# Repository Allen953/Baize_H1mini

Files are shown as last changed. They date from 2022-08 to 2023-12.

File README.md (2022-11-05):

# Baize_HexapodRobot_Arduino

$\color{red}{DIY交流群：902595482。}$

实际上这个机械结构是国外老哥做的一款arduino六足机器人。

这里我们结合ROS做运动学解算，做一些控制步态和算法，提供更多丰富的功能。

目前主要用arduino和ros两种软件平台来做，可以用于学习arduino或者ros编程，同时也可以将ros于arduino结合。

arduino端主要跑驱动，ros端跑步态算法等。实际上只要arduino也可以工作，用遥控控制即可。

如下图是实物图：

实物图1

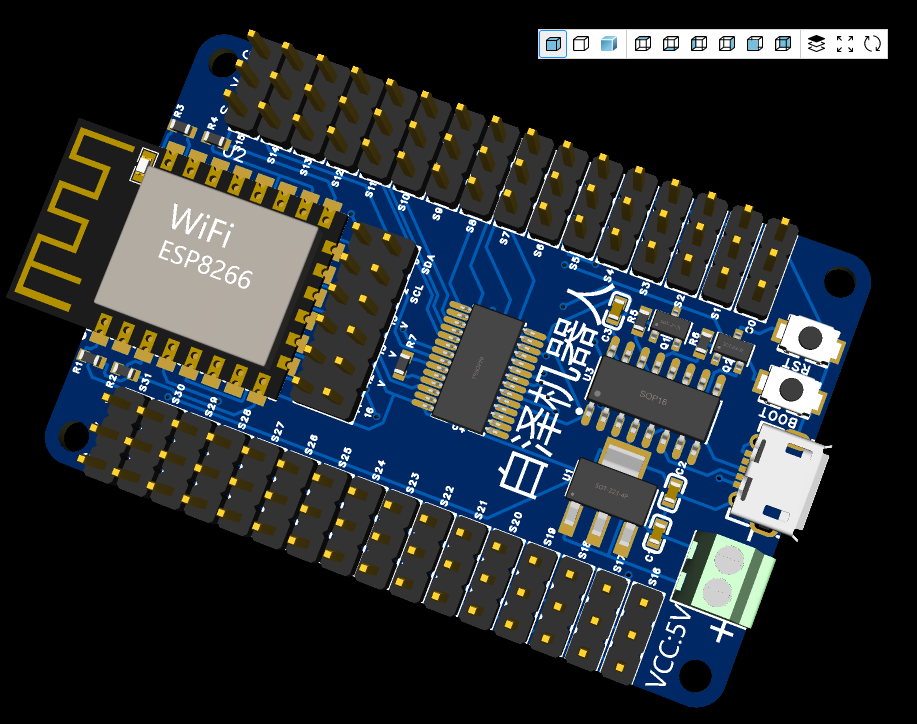
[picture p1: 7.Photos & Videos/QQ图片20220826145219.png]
主控板


ROS下步态规划:

仿真图

俯视图:

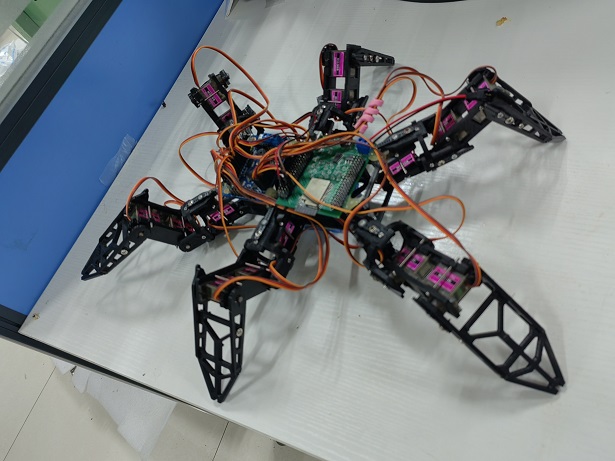
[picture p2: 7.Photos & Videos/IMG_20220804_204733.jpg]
实物图2


RVIZ预览图1
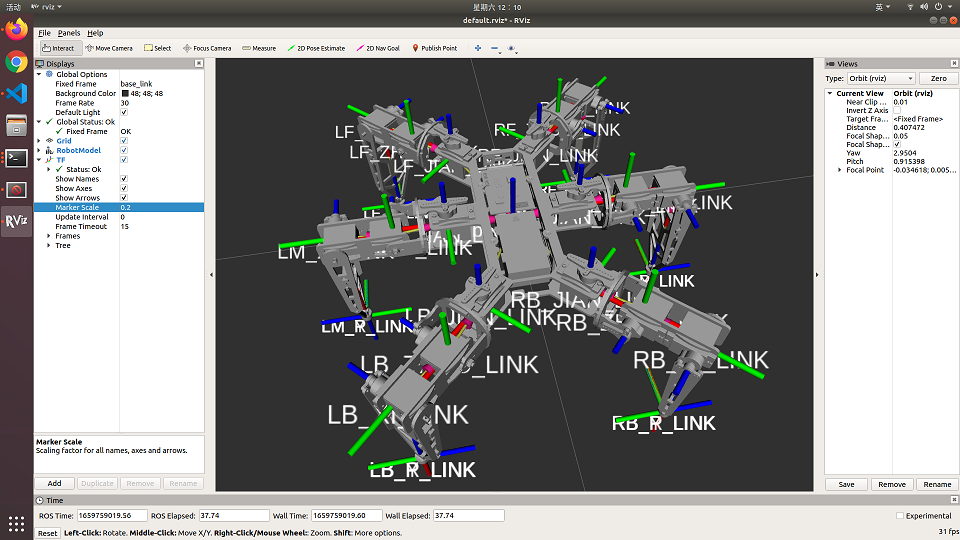
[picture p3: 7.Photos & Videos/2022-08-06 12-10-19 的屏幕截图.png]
RVIZ预览图1


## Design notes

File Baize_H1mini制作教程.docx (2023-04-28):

Baize_H1mini制作教程

作者：Allen

## 一.项目介绍

代码：https://gitee.com/li9535/baize_hexapod-robot

最新代码在这里：

Arduino版：https://github.com/Allen953/Baize_HexapodRobot_Arduino

ROS版：https://github.com/Allen953/Baize_HexapodRobot_ROS

实际上这个机械结构是国外老哥做的一款arduino六足机器人。

这里我们把他改造成ros和arduino两个版本的，提供更多丰富的功能。

下面我们在这个项目后面加上“_arduino”和"_ros"的后缀来区分arduino和ros两个版本。

再在后面加上"_v1"来表示版本号。

例如:“白泽六足机器人_arduino_v1”就是表示这个是arduino版本的第一版。

目前主要用arduino和ros两种软件平台来做，可以用于学习arduino或者ros编程，同时也可以将ros于arduino结合。

最初这个机器人用的也是arduino mega2560当主控，外加一块舵机驱动板，如下图

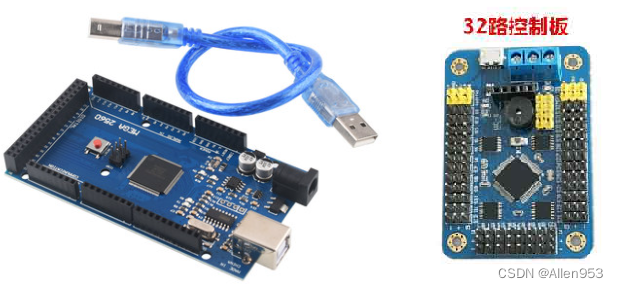
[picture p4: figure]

编辑

在新版本中，我们摒弃传统的开发板+舵机驱动板的方式。开发板+舵机驱动板的方式一个方面是集成度不高，杜邦线接线麻烦且可靠性差。另一个方面，两块板子成本加起来也要将近200块，实在是浪费。

所以我们自己做了两版舵机驱动板，用esp8266或者esp32做主控，更低的成本，更强大的性能，更丰富的功能且支持WiFi无线遥控，实在是香！

他们分别是采用esp8266做主控的Baize_ServoDriver_esp8266 (https://github.com/Allen953/Baize_ServoDriver_esp8266)和采用esp32做主控的Baize_ServoDriver_esp32。

如下图，都是开源的，点击项目名称即可跳转到开源链接。

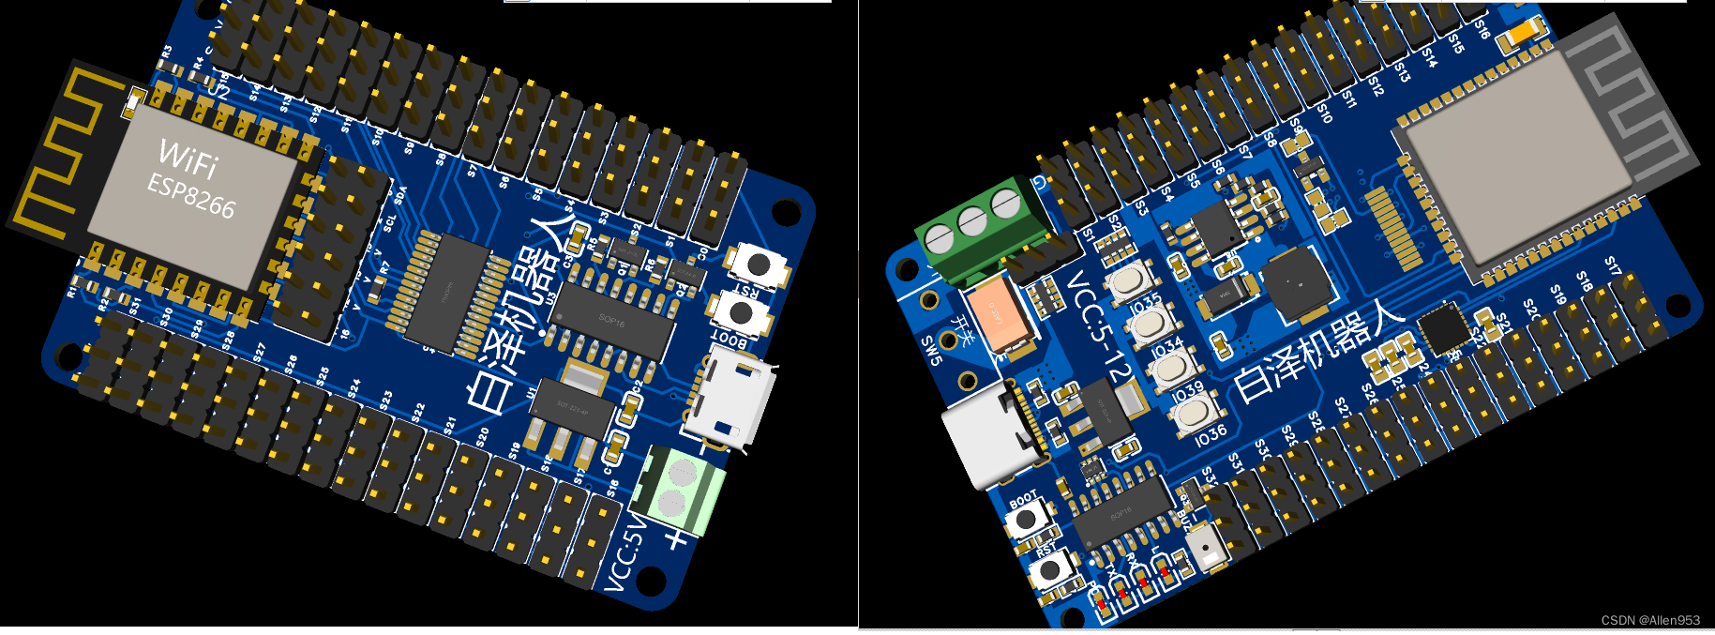
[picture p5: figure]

编辑

实物图

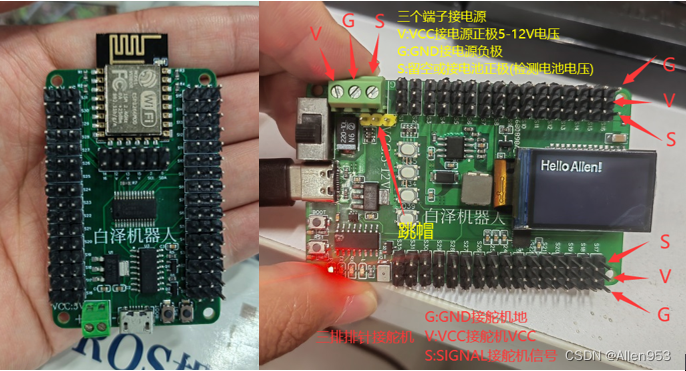
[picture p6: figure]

编辑

两个版本的机器人外观大致如下图所示：

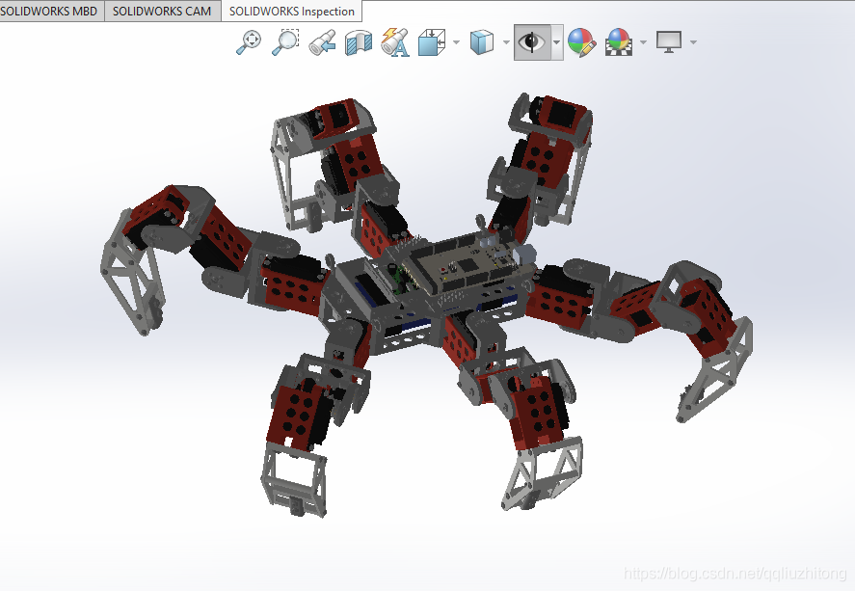
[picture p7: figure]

## 二.Baize_H1mini制作组装机器人机械结构

### 1.组装调试教程

### （1）零件准备 (https://blog.csdn.net/qqliuzhitong/article/details/118224735)

1.主控板x1

Baize_ServoDriver_esp8266 (https://github.com/Allen953/Baize_ServoDriver_esp8266)或者Baize_ServoDriver_esp32 (https://github.com/Allen953/Baize_ServoDriver_esp32)

如下图左边为 Baize_ServoDriver_esp8266；右边为Baize_ServoDriver_esp32

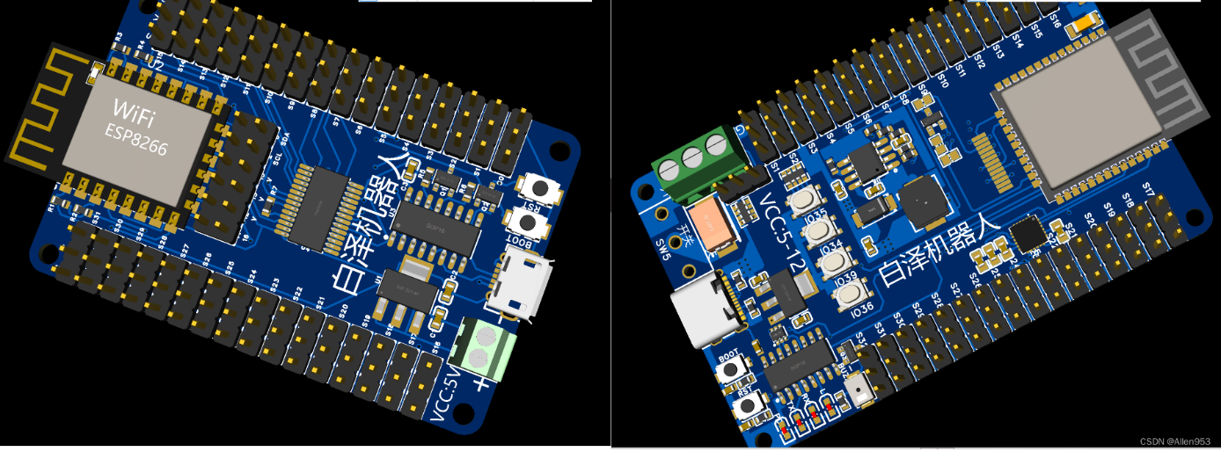
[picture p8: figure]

编辑

建议arduino版六足用Baize_ServoDriver_esp8266而ROS版六足用Baize_ServoDriver_esp32。

我们这里是做arudino版，所以就默认为Baize_ServoDriver_esp8266。

2.机械零件

链接：GitHub - Allen953/Baize_HexapodRobot_Arduino (https://github.com/Allen953/Baize_HexapodRobot_Arduino)

在如下目录下即可下载到

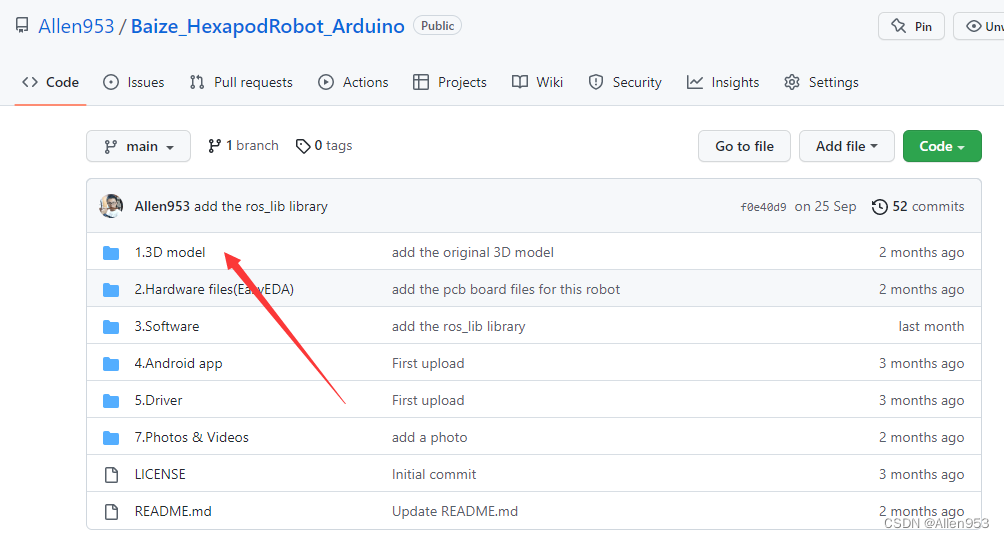
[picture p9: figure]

编辑

编辑

4.舵机x18

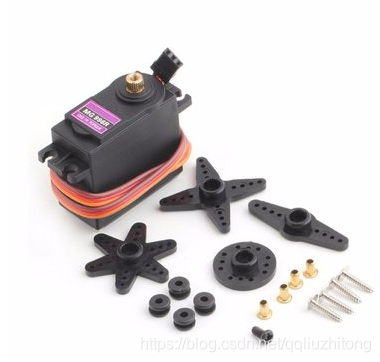
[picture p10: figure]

编辑

5.轴承

624ZZ

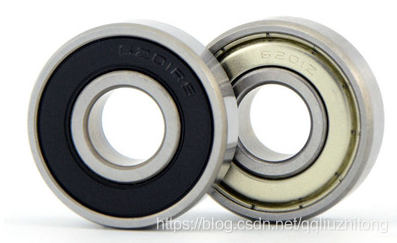
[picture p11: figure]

编辑

6.电池

电池要买大功率电池，7.4V的大电流电池。

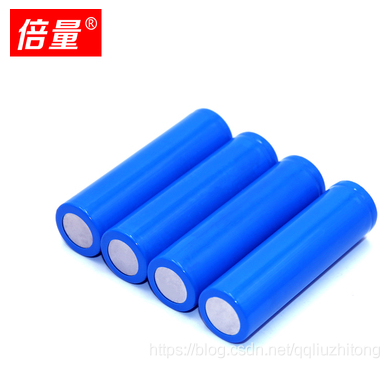
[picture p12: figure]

编辑

7.螺丝

螺丝主要有两种，一种是M3*10，一种是M3*12。下面是螺丝型号及数量。

M3*10——200个

M3*12——200个

### （2）白泽舵机驱动板 (https://blog.csdn.net/qqliuzhitong/article/details/124497060)

这是一块32路舵机驱动板，做舵机机器人非常方便。主控用的esp8266.

电源用的5V的电池，电池直接给舵机供电，经过压降之后产生3.3V电压给esp8266模组供电。

这块板儿主要是用于控制sg90舵机，就是那种蓝色舵机，或者mg90s舵机。

后续会升级，升级后可以控制5-12V的pwm舵机。

这样就可以控制高压的舵机，比如型号为mg996r或mg995的舵机。

3D图片如下图所示：

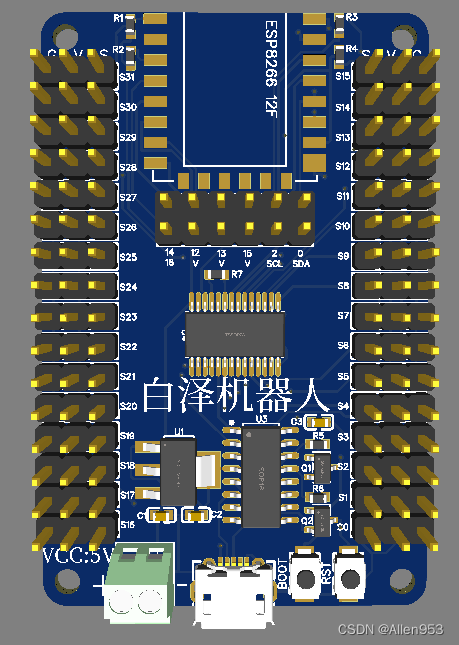
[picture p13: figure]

编辑

实物图如下：

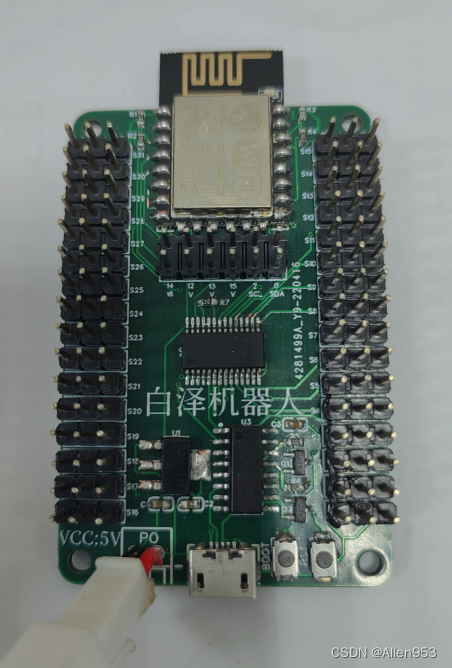
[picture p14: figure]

编辑

#### 测试代码：

#### 例程1：控制32路舵机匀速旋转从0-180度

/*******************************************************

主板：Baize_ServoDriver_esp8266 开源链接：https://github.com/Allen953/Baize_ServoDriver_esp8266

功能：控制32路舵机匀速旋转从0-180度

引脚：SDA:21 SCL:22

Designer: Allen

E-mail:953598974@qq.com

Date:2022-08-24

*******************************************************/

#include <Wire.h>

#include <Adafruit_PWMServoDriver.h>

Adafruit_PWMServoDriver pwm = Adafruit_PWMServoDriver();

Adafruit_PWMServoDriver pwm1 = Adafruit_PWMServoDriver(0x41);

#define SERVOMIN 102 //0.5/20 * 4096 = 102

#define SERVOMAX 512 //2.5/20 * 4096 = 512

void setup() {

Serial.begin(115200);

Serial.println();

Serial.println("16 channel Servo test!");

pwm.begin();

pwm1.begin();

pwm.setPWMFreq(50); // Analog servos run at ~50 Hz updates

pwm1.setPWMFreq(50); // Analog servos run at ~50 Hz updates

delay(200);

for(int i=0;i<16;i++)

{

pwm.setPWM(i, 0, SERVOMIN); // 驱动32路舵机转到0度

pwm1.setPWM(i, 0, SERVOMIN);// 驱动32路舵机转到0度

}

delay(2000);

for (uint16_t pulselen = SERVOMIN; pulselen < SERVOMAX; pulselen++) {

for(int i=0;i<16;i++)

{

pwm.setPWM(i, 0, pulselen);

pwm1.setPWM(i, 0, pulselen);

}

delayMicroseconds(200);

ESP.wdtFeed(); //喂狗防止复位

}

}

void loop() {

}

#### 例程2：控制32路舵机匀速旋转从0-180度，再从180-0度

/*******************************************************

主板：Baize_ServoDriver_esp8266 开源链接：https://github.com/Allen953/Baize_ServoDriver_esp8266

功能：控制32路舵机匀速旋转从0-180度，再从180-0度

引脚：SDA:21 SCL:22

Designer: Allen

E-mail:953598974@qq.com

Date:2022-08-24

*******************************************************/

#include <Wire.h>

#include <Adafruit_PWMServoDriver.h>

Adafruit_PWMServoDriver pwm = Adafruit_PWMServoDriver();

Adafruit_PWMServoDriver pwm1 = Adafruit_PWMServoDriver(0x41);

#define SERVOMIN 102 //0.5/20 * 4096 = 102

#define SERVOMAX 512 //2.5/20 * 4096 = 512

void setup() {

Serial.begin(115200);

Serial.println("16 channel Servo test!");

pwm.begin();

pwm1.begin();

pwm.setPWMFreq(50); // Analog servos run at ~50 Hz updates

pwm1.setPWMFreq(50); // Analog servos run at ~50 Hz updates

}

void loop() {

for (uint16_t pulselen = SERVOMIN; pulselen < SERVOMAX; pulselen++) {

for(int i=0;i<16;i++)

{

pwm.setPWM(i, 0, pulselen);

pwm1.setPWM(i, 0, pulselen);

}

delayMicroseconds(200);

ESP.wdtFeed(); //喂狗防止复位

}

for (uint16_t pulselen = SERVOMAX; pulselen > SERVOMIN; pulselen--) {

for(int i=0;i<16;i++)

{

pwm.setPWM(i, 0, pulselen);

pwm1.setPWM(i, 0, pulselen);

}

delayMicroseconds(200);

ESP.wdtFeed(); //喂狗防止复位

}

}

#### 例程3：控制32路舵机从0，90，180，90，0度之间循环。

/*******************************************************

主板：Baize_ServoDriver_esp8266 开源链接：https://github.com/Allen953/Baize_ServoDriver_esp8266

功能：控制32路舵机从0，90，180，90，0度之间循环

引脚：SDA:21 SCL:22

Designer: Allen

E-mail:953598974@qq.com

Date:2022-08-24

*******************************************************/

#include <Wire.h>

#include <Adafruit_PWMServoDriver.h>

Adafruit_PWMServoDriver pwm = Adafruit_PWMServoDriver();

Adafruit_PWMServoDriver pwm1 = Adafruit_PWMServoDriver(0x41);

#define SERVOMIN 102 //0.5/20 * 4096 = 102

#define SERVOMID 307 //(102+512)/2=307

#define SERVOMAX 512 //2.5/20 * 4096 = 512

//pwm.setPWM(i, 0, pulse);i=0~15对应第0-15个舵机；pwm1.setPWM(j, 0, pulse);j=0~15对应第16-31个舵机，

void setup() {

Serial.begin(115200);

Serial.println("16 channel Servo test!");

pwm.begin();

pwm1.begin();

pwm.setPWMFreq(50); // Analog servos run at ~50 Hz updates

pwm1.setPWMFreq(50); // Analog servos run at ~50 Hz updates

}

void loop() {

//全部舵机转到0度

for(int i=0;i<16;i++)

{

pwm.setPWM(i, 0, SERVOMIN);

pwm1.setPWM(i, 0, SERVOMIN);

}

delayMicroseconds(200);

ESP.wdtFeed(); //喂狗防止复位

delay(1000);

//全部舵机转到90度

for(int i=0;i<16;i++)

{

pwm.setPWM(i, 0, SERVOMID);

pwm1.setPWM(i, 0, SERVOMID);

}

delayMicroseconds(200);

ESP.wdtFeed(); //喂狗防止复位

delay(1000);

//全部舵机转到180度

for(int i=0;i<16;i++)

{

pwm.setPWM(i, 0, SERVOMAX);

pwm1.setPWM(i, 0, SERVOMAX);

}

delayMicroseconds(200);

ESP.wdtFeed(); //喂狗防止复位

delay(1000);

//全部舵机转到90度

for(int i=0;i<16;i++)

{

pwm.setPWM(i, 0, SERVOMID);

pwm1.setPWM(i, 0, SERVOMID);

}

delayMicroseconds(200);

ESP.wdtFeed(); //喂狗防止复位

delay(1000);

}

#### 例程4：板子连到手机热点

手机需要开一个热点，名字："Baize"，密码："baizerobot"。

然后上传这个程序到板子上，在手机上就能看到板子连到手机热点了。

//修改自：https://blog.csdn.net/wangke0809/article/details/70146378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

//原作者：wangke0809

#include <ESP8266WiFi.h>

#define MAX_SRV_CLIENTS 3 //最大同时联接数，即你想要接入的设备数量，8266tcpserver只能接入五个，哎

const char *ssid = "Baize";

const char *password = "baizerobot";

WiFiServer server(8266);//你要的端口号，随意修改，范围0-65535

WiFiClient serverClients[MAX_SRV_CLIENTS];

void setup()

{

Serial.begin(9600);

delay(10);

pinMode(16, OUTPUT);

digitalWrite(16, 0);

WiFi.begin(ssid, password);

while (WiFi.status() != WL_CONNECTED)

{

delay(500);

}

server.begin();

server.setNoDelay(true); //加上后才正常些

}

void loop()

{

blink();

uint8_t i;

if (server.hasClient())

{

for (i = 0; i < MAX_SRV_CLIENTS; i++)

{

if (!serverClients[i] || !serverClients[i].connected())

{

if (serverClients[i]) serverClients[i].stop();//未联接,就释放

serverClients[i] = server.available();//分配新的

continue;

}

}

WiFiClient serverClient = server.available();

serverClient.stop();

}

for (i = 0; i < MAX_SRV_CLIENTS; i++)

{

if (serverClients[i] && serverClients[i].connected())

{

digitalWrite(16, 0);//有链接存在,就一直长亮

if (serverClients[i].available())

{

while (serverClients[i].available())

Serial.write(serverClients[i].read());

}

}

}

if (Serial.available())

{

size_t len = Serial.available();

uint8_t sbuf[len];

Serial.readBytes(sbuf, len);

//push UART data to all connected telnet clients

for (i = 0; i < MAX_SRV_CLIENTS; i++)

{

if (serverClients[i] && serverClients[i].connected())

{

serverClients[i].write(sbuf, len); //向所有客户端发送数据

delay(1);

}

}

}

}

void blink()

{

static long previousMillis = 0;

static int currstate = 0;

if (millis() - previousMillis > 200) //200ms

{

previousMillis = millis();

currstate = 1 - currstate;

digitalWrite(16, currstate);

}

}

#### 例程5：发现（校验）板子上的iic设备

/*******************************************************

主板：Baize_ServoDriver_esp8266 开源链接：https://github.com/Allen953/Baize_ServoDriver_esp8266

功能：扫描IIC总线上挂载的设备

引脚：SDA:21 SCL:22

Designer: Allen

E-mail:953598974@qq.com

Date:2022-08-24

*******************************************************/

#include <Wire.h>

void setup()

{

Wire.begin();

Serial.begin(115200);

}

void loop()

{

byte error, address;

int nDevices;

Serial.println();

Serial.println("Scanning...");

nDevices = 0;

for(address = 1; address < 127; address++ )

{

Wire.beginTransmission(address);

error = Wire.endTransmission();

if (error == 0)

{

Serial.print("I2C device found at address 0x");

if (address<16)

Serial.print("0");

Serial.print(address,HEX);

Serial.println(" !");

nDevices++;

}

else if (error==4)

{

Serial.print("Unknown error at address 0x");

if (address<16)

Serial.print("0");

Serial.println(address,HEX);

}

}

if (nDevices == 0)

Serial.println("No I2C devices found\n");

else

Serial.println("done\n");

delay(5000);

}

#### 例程6：带电压监测的板子测试程序

升级版，主控esp32。供电范围5-12V。当我用7.4V的2S锂电池给舵机供电时，用这个程序来进行板子测试，由于测试时间较长，担心电池过放，所以通过电压监测，当电压过低时，将不再驱动舵机工作。

/***************************************************

对于ARDUINO UNO，这时SCL->A5，SDA - >A4

对于ESP8266，这时SCL->GPIO5，SDA - >GPIO4

****************************************************/

#include <Wire.h>

#include <Adafruit_PWMServoDriver.h>

Adafruit_PWMServoDriver pwm = Adafruit_PWMServoDriver();

Adafruit_PWMServoDriver pwm1 = Adafruit_PWMServoDriver(0x41);

#define SERVOMIN 102 //0.5/20 * 4096 = 102

#define SERVOMAX 512 //2.5/20 * 4096 = 512

//pcb板测试时，如果是2S的锂电池供电，则以此电压为阈值，低于此电压时，不再驱动舵机运动，保护电池。

float voltage_threshold = 6.5;

int voltage_testpin = 26;

float voltage_b = 0.0;

bool servo_f = 1;

void setup() {

Serial.begin(115200);

Serial.println();

Serial.println("16 channel Servo test!");

pwm.begin();

pwm1.begin();

pwm.setPWMFreq(50); // Analog servos run at ~50 Hz updates

pwm1.setPWMFreq(50); // Analog servos run at ~50 Hz updates

delay(200);

for(int i=0;i<16;i++)

{

pwm.setPWM(i, 0, SERVOMIN); // 驱动32路舵机转到0度

pwm1.setPWM(i, 0, SERVOMIN);// 驱动32路舵机转到0度

}

delay(2000);

for (uint16_t pulselen = SERVOMIN; pulselen < SERVOMAX; pulselen++) {

for(int i=0;i<16;i++)

{

pwm.setPWM(i, 0, pulselen);

pwm1.setPWM(i, 0, pulselen);

}

delayMicroseconds(200);

}

}

void loop() {

if(servo_f==1)

{

for (uint16_t pulselen = SERVOMIN; pulselen < SERVOMAX; pulselen++) {

for(int i=0;i<16;i++)

{

pwm.setPWM(i, 0, pulselen);

pwm1.setPWM(i, 0, pulselen);

}

delayMicroseconds(200);

}

//电压检测

int voltage_sum = 0.0;

for(int i=0;i<10;i++)

{

voltage_sum += float(analogRead(voltage_testpin))/4095.0*3.3*4.0;

Serial.println(analogRead(voltage_testpin));

delay(100);

}

voltage_b = voltage_sum / 10.0;

Serial.println(voltage_b);

if(voltage_b<voltage_threshold)

servo_f = 0;

for(int i=0;i<16;i++)

{

pwm.setPWM(i, 0, SERVOMIN); // 驱动32路舵机转到0度

pwm1.setPWM(i, 0, SERVOMIN);// 驱动32路舵机转到0度

}

delay(2000);

}

}

#### 例程7：串口控制舵机角度

/*******************************************************

主板：Baize_ServoDriver_esp8266 开源链接：https://github.com/Allen953/Baize_ServoDriver_esp8266

功能：串口输入角度，板子驱动舵机转到该角度

引脚：SDA:21 SCL:22

Designer: Allen

E-mail:953598974@qq.com

Date:2022-08-24

*******************************************************/

#include <Wire.h>

#include <Adafruit_PWMServoDriver.h>

Adafruit_PWMServoDriver pwm = Adafruit_PWMServoDriver(); //驱动1~16或(0~15)号舵机

Adafruit_PWMServoDriver pwm1 = Adafruit_PWMServoDriver(0x41); //驱动17~32或(16~31)号舵机

//#define SERVOMIN 102 //0.5/20 * 4096 = 102

//#define SERVOMID 307 //1.5/20 * 4096 = 307

//#define SERVOMAX 512 //2.5/20 * 4096 = 512

//实际测试

#define SERVOMIN 102

#define SERVOMID 327

#define SERVOMAX 552

void setup() {

// put your setup code here, to run once:

Serial.begin(115200);

pwm.begin();

pwm1.begin();

pwm.setPWMFreq(50); // Analog servos run at ~50 Hz updates

pwm1.setPWMFreq(50); // Analog servos run at ~50 Hz updates

}

void loop() {

// put your main code here, to run repeatedly:

while(!(Serial.available()>0))ESP.wdtFeed();//喂狗防止复位

int pwmsum=Serial.parseInt();

for(int i=0;i<16;i++)

{

pwm.setPWM(i, 0, pwmsum);

}

pwm1.setPWM(0, 0, pwmsum);

pwm1.setPWM(1, 0, pwmsum);

delay(100);

}

#### 固件烧录

有些小伙伴没有安装好arduino ide或者没有安装好esp8266的硬件支持包，这个时候呢，就没法编译程序进行烧录了。

所以我在资料文件夹里面放上了编译好的固件，咱们就无需编译直接使用烧录工具就可以把固件给烧录到板子上了。

找到烧录工具并打开

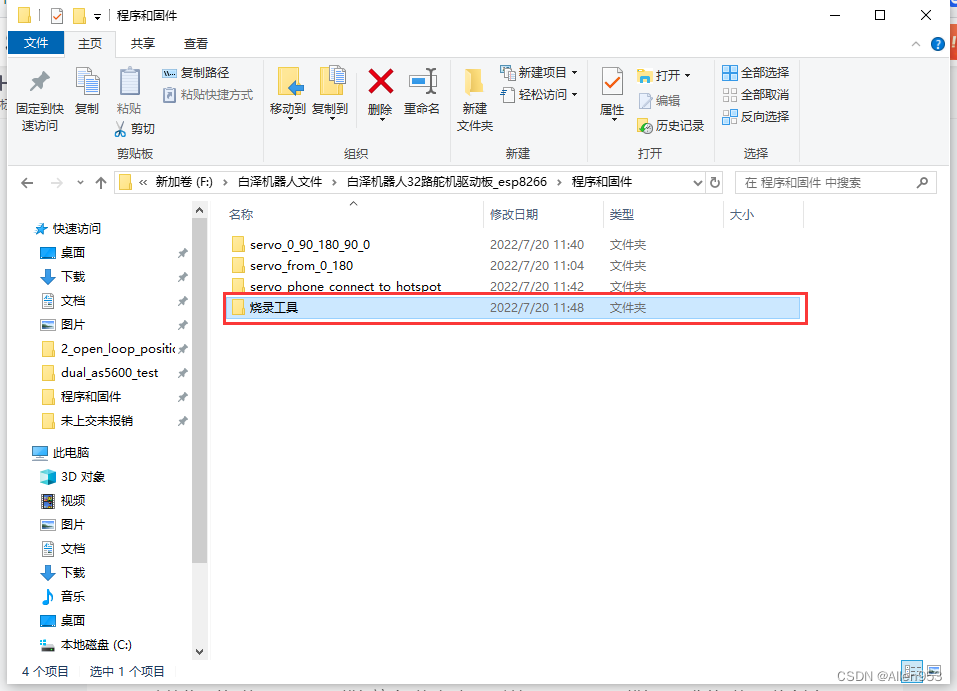
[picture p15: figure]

编辑

打开烧录程序

编辑

选中com口

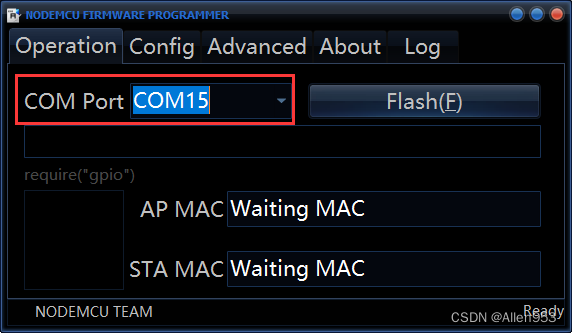
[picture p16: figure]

编辑

点击齿轮选中要烧录的固件(.bin格式)，填写烧录地址，并在要烧录的固件前面打勾。

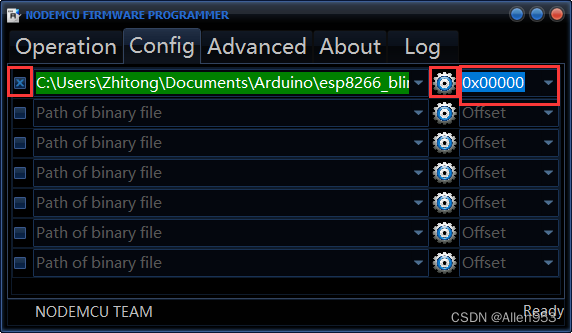
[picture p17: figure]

编辑

选择上传的波特率，flash大小，flash速度等。

然后点击flash进行烧录，烧录完成后，进度条会跑满，左下角会出现绿色打勾符号。

按一下板子上的rst按键，重启板子，程序就开始执行了。

#### 我遇到的问题

##### 1.插电脑不出com口，怎么操作都没用

ch340芯片焊错了，焊成了ch340g芯片，导致usb-ttl芯片无法正常工作。

##### 2.插电脑不出com口，按住rst按键会出com口，松开又消失

原因是台式机电脑前面的usb口能供应的电流太小了，带不起来板子。

当按住rst的时候，esp8266模组这个时候相当于是关机了，esp8266模组不工作的时候，整个板子自然功耗下降下来，然后ch340c芯片工作正常，这样一来电脑就出com口了。

而一旦松开rst，这个时候esp8266模组要开始工作，板子功耗又起来了，usb口带不动过载了，所以ch340c芯片无法正常工作，com口就消失了。

### （3）3D打印开源六足机器人程序 (https://blog.csdn.net/qqliuzhitong/article/details/116492164)

### 2.编程例程

持续更新中！！！！！！！

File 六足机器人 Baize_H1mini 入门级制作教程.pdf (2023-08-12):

# 六足机器人 Baize_H1mini 入门级制作教程

## 作者：人民群众

版本：20230723

Baize_H1mini 六足机器人是一个创客学习平台，通过该学习平台，可以学 习 mixly 图形化编程，Arduino 平台的 C 语言编程，ROS 机器人编程，也可以学 习一些传感器的控制。
在 Baize_H1mini 中，我们摒弃传统的开发板+舵机驱动板的方式。开发板+ 舵机驱动板的方式一方面集成度不高，杜邦线接线麻烦且可靠性差；另一方面， 集成板降低了电器元件的成本，让机器人制作更加方便。

我们有一个 QQ 交流群：902595482，可以进来互相学习。 jiaoliuqun:902595482

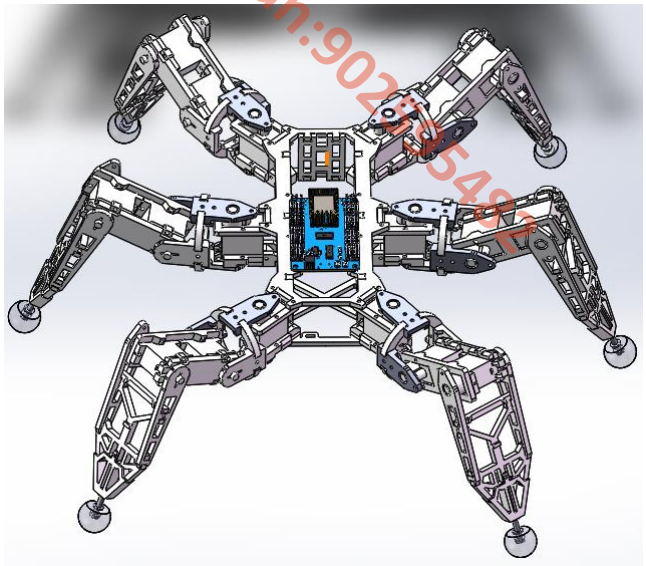
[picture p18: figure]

### 重要提示

1.电池一定要小心接，最好反复确认自己理解了电源部分是怎么接线

的，然后再通电；否则不能随便通电，以免短路起火或发生爆炸。

2.对于新手来讲，一定要认真阅读理解本教程，不能一目十行不仔细

阅读文字说明只看图片，这将会导致很多步骤理解不到。

3.在碰到不懂且说明书上没有的内容时，一定要善于用百度进行搜索 且多多尝试。jiaoliuqun:902595482 （也可以在群里问，推荐在群里提问！）

### 一.项目介绍

1.项目介绍

最新代码在这里：https://github.com/Allen953/Baize_H1mini 实际上这个机械结构是国外老哥做的一款 arduino 六足机器人。 这里我们把他改造成 arduino 版本的，提供更多丰富的功能。目前主要用 arduino 和 ros 两种软件平台来做，可以用于学习 arduino 或者 ros 编程，同时 也可以将 ros 于 arduino 结合。
在这个六足机器人的制作中，我们摒弃传统的开发板+舵机驱动板的方式。

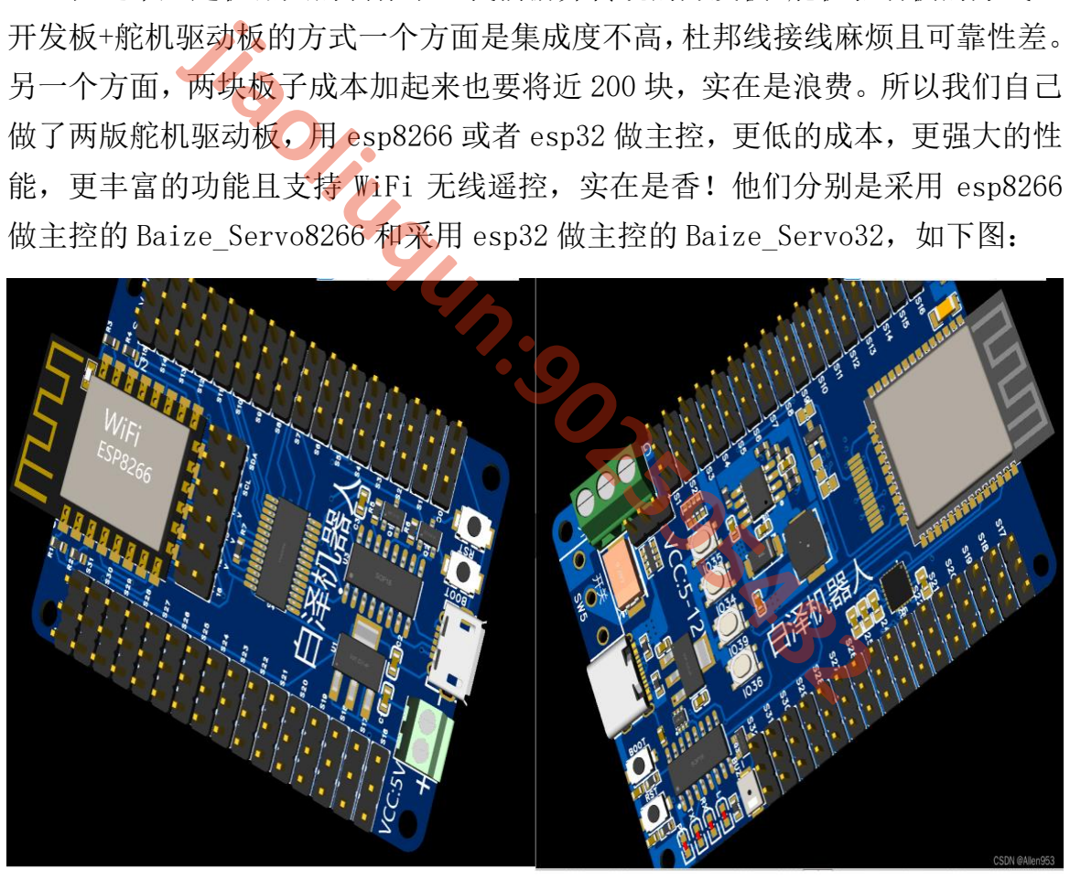
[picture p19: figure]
jiaoliuqun:902595482

开发板+舵机驱动板的方式一个方面是集成度不高，杜邦线接线麻烦且可靠性差。 另一个方面，两块板子成本加起来也要将近 200 块，实在是浪费。所以我们自己 做了两版舵机驱动板，用 esp8266 或者 esp32 做主控，更低的成本，更强大的性 能，更丰富的功能且支持 WiFi 无线遥控，实在是香！他们分别是采用 esp8266 做主控的 Baize_Servo8266 (https://github.com/Allen953/Baize_ServoDriver_esp8266) 和采用 esp32 做主控的 Baize_Servo32，如下图： (https://github.com/Allen953/Baize_ServoDriver_esp32)

实物图

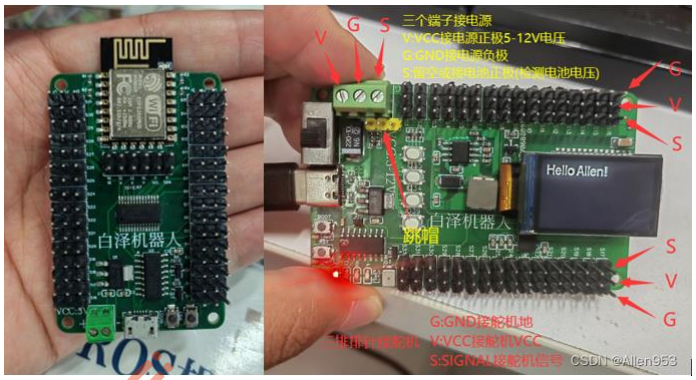
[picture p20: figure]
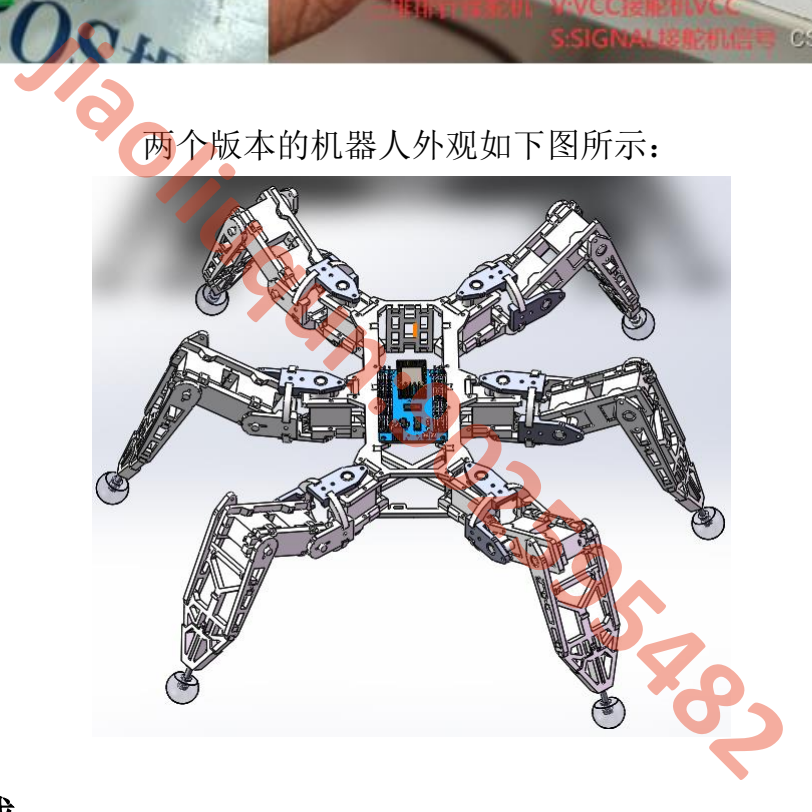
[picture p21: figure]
jiaoliuqun:902595482

两个版本的机器人外观如下图所示：

2.资料下载

在开始制作该项目前，最好将所有的资料先下载到自己的电脑上，你需要按 照以下步骤来下载该项目需要用到的全部资料：
首 先 访 问 项 目 网 页 ： https://github.com/Allen953/Baize_H1mini

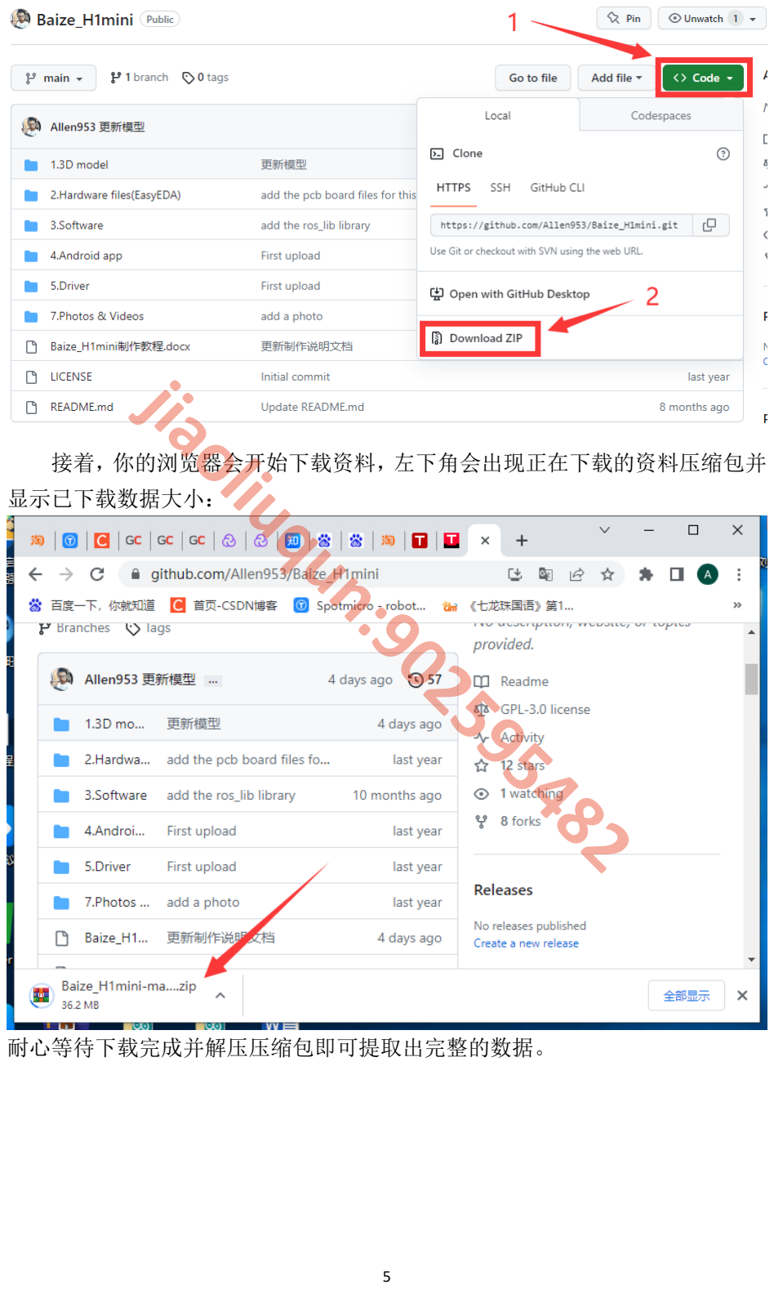
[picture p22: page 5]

接着，你的浏览器会开始下载资料，左下角会出现正在下载的资料压缩包并 显示已下载数据大小：

耐心等待下载完成并解压压缩包即可提取出完整的数据。

# jiaoliuqun:902595482

二.Baize_H1mini 机器人零件制作准备

1.机械结构零件打印制作

重要提示：自己使用打印机打印零件时，对于新手来说肯定会由于参数设置 问题将零件打废，因此要仔细配置参数确保参数正确。对于需要添加支撑的零 件，一定要记得添加支撑。
首先要找到零件的图纸，打开我们刚刚下载的整个项目资料文件夹，找到如 下路径 1.3D model\Baize_HexapodRobot_Arduino_3DPrinter\STL Files，可以 看到该文件夹下有很多可以打印的 STL 格式图纸，如下图红框中所示：

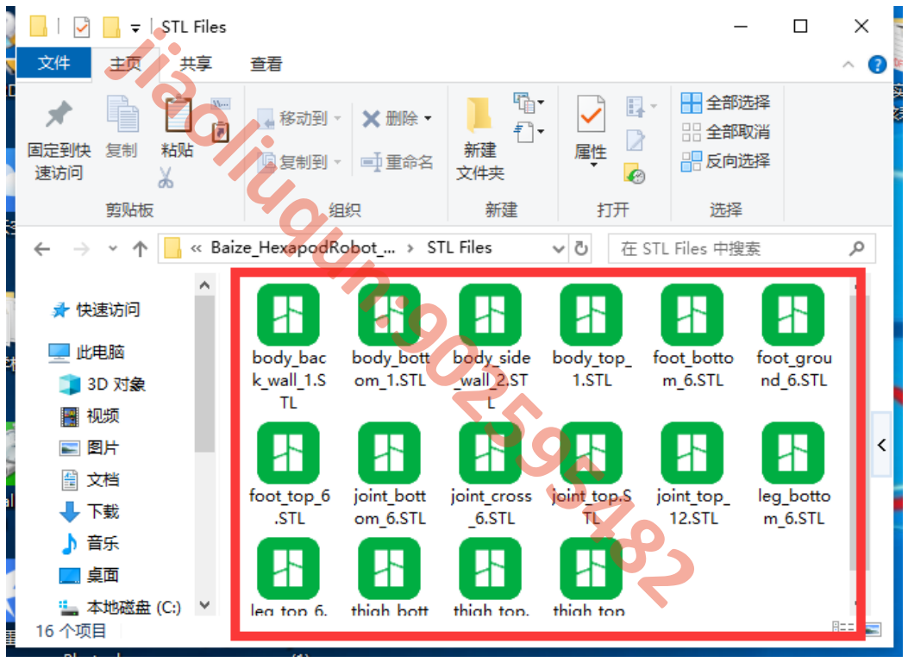
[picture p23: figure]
jiaoliuqun:902595482

接下来就可以开始打印了，我这里用的是拓竹 P1P 型号 3D 打印机，因此下 面的打印教程也是用该款型号打印机制作的，如果你用的其他型号的 3D 打印机， 则可以一次做参考并参照自己 3D 打印机的说明书进行打印。
下载 Bambu Studio：http:bambulab.com/download
登录 Bambu Stidio，新建或打开一个项目。

添加一个模型进行模型切片。
完成模型切片后，选择打印机并发送打印。
打印板类型选择纹理 PEI 打印板

打印材料是啥？ PLA 3D 打印材料一般有 PLA 和 ABS 两款材料

这里需要选择打印材料。

# jiaoliuqun:902595482

2.主控板 PCB 制作及焊接

3.标准件准备（包括螺丝和电器原件等）

1..舵机 x18

2.电池

电池要买 18650 大功率电池，单节电池是 3.7V 左右（之所以说是 3.7V 左右 而不是 3.7V 是因为电池电压随着使用过程会发生改变，当单节电池充满电时大 多数在 4.2V 左右，当电池放电到没电状态之后，电池电压会下降到 3.7V 甚至 3.2V，电池电压下降到 3.2V 的时候就要充电了，如果电池电压下降太多，可能

# jiaoliuqun:902595482

会发生永久性的损坏充不了电，因此在使用过成功要及时为电池充电以免电池损 坏），这里我们两节串联起来使用，加起来就是 7.2V 左右。

3.螺丝等标准件

螺丝一共有以下几种：下面是螺丝型号及数量
M2*30——36 个
M2*8——12 个
M2*15——6 个
M2*5——42 个
圆柱销φ4*12——18 个

4.LM2596S 压降模块

这个压降模块可以将 2 节 18650 电池的 7.4~8.4V 电压降至 5V 电压，由于我

们的板子供电电压是 5V，而且舵机供电电压也是 5V，因此需要用到这个模块。 jiaoliuqun:902595482

# jiaoliuqun:902595482

三.Baize_H1mini 机器人组装

1.零件准备 (https://blog.csdn.net/qqliuzhitong/article/details/118224735)

1.主控板 x1
Baize_ServoDriver_esp8266 (https://github.com/Allen953/Baize_ServoDriver_esp8266) 或者 Baize_ServoDriver_esp32 (https://github.com/Allen953/Baize_ServoDriver_esp32)
如下图左边为 Baize_ServoDriver_esp8266 ；右边为 Baize_ServoDriver_esp32

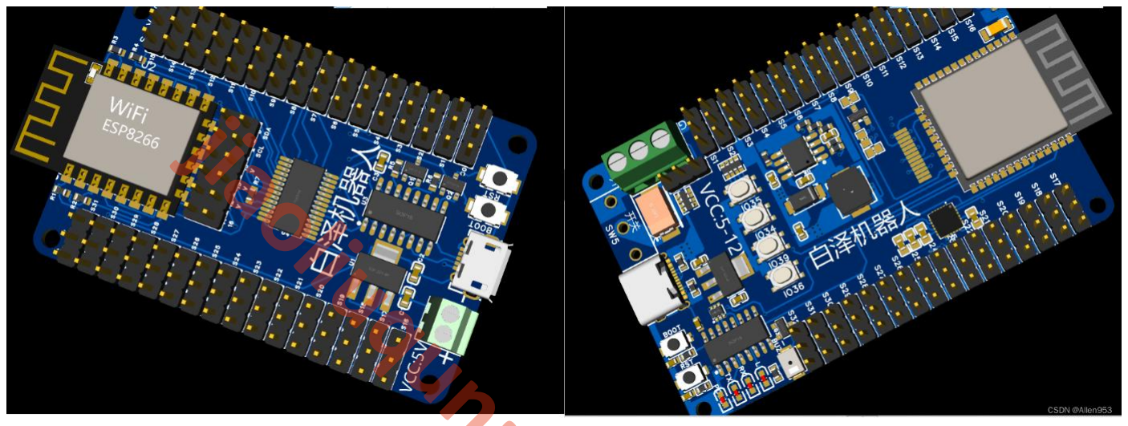
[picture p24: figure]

建议 arduino 版六足用 Baize_ServoDriver_esp8266 而 ROS 版六足用 Baize_ServoDriver_esp32。
我们这里是做 arudino 版，所以就默认为 Baize_ServoDriver_esp8266。

2.机械零件

链接：https://github.com/Allen953/Baize_H1mini

在如下目录下即可下载到 jiaoliuqun:902595482

2.组装教程

找到下面的φ4*12 的金属圆柱销，然后将圆柱销用力塞进或者敲进打印的零件 里面

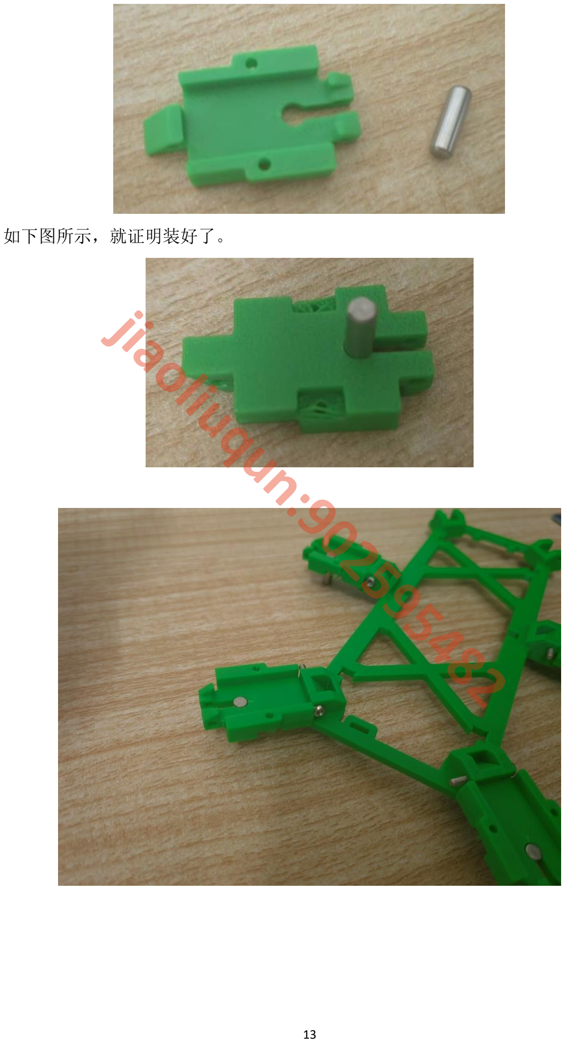
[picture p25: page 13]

如下图所示，就证明装好了。

# jiaoliuqun:902595482

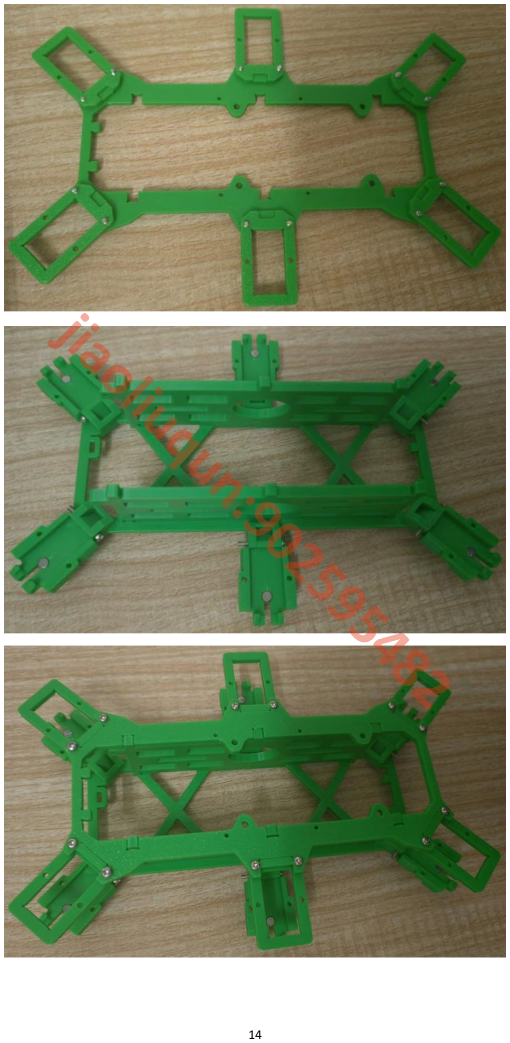
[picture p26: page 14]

# jiaoliuqun:902595482

3.电路焊接

首先，需要找一个 18650 电池的电池盒，由于电池盒上面直接引出来了两条 线，这两条电源线是先输入到 LM2596S 这个压降模块的，需要先降压到 5V。由 于直接把电池盒上面的两条电源线焊接在 LM2596S 模块上那就进行了通电，而无 法断电，因此需要一个开关。我们现在的做法是在电池的输出端和 LM2596S 的输 入端各焊一个插接口的电源线，这样可以通过插拔的方式给整个电路通电和断电， 起到开关的作用。

接着需要焊接 LM2596S 的输入和输出线

LM2596S 压降模块的作用就是把电压降至 5V，电流从电池里面出来的时候是 7.4V， 进入该模块的时候也是 7.4V，从该模块出来的时候，电压就变成 5V 了，就可以 输入到机器人板子上了。整个电源部分工作原理如下图所示,LM2596S 模块的 IN+ 表示输入正极，IN-表示输入负极，也就是电池的电从这两个地方输入到模块； OUT+表示的是输出负极，OUT-表示的是输出正极，输出的 5V 电压从这里流出去。

电源线红色是正极，黑色是负极。

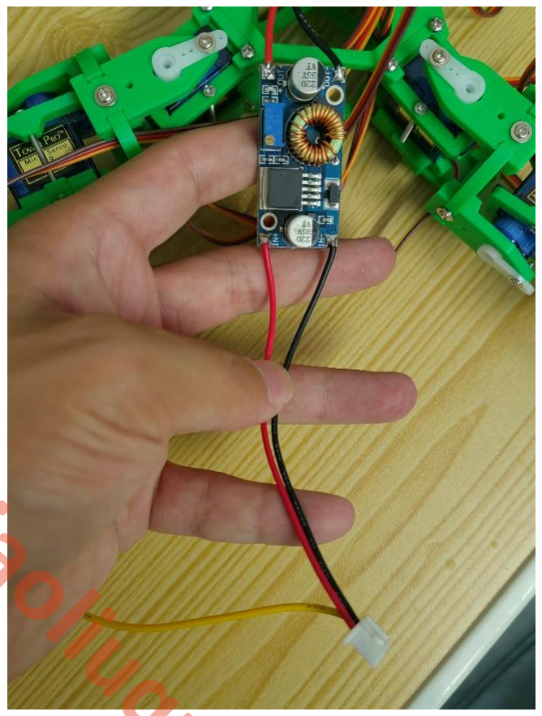
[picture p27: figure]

接下来，就可以直接把电池的输出接口插在 LM2596 的输入接口了，这个时 候先别着急把 LM2596S 模块的输出接口接到舵机控制板上面，如下图所示，红色 打叉号的两条线先断开别接上。因为 LM2596S 模块的输出电压我们还没调节，默 认情况下 LM2596S 模块的输出电压太高，我们如果直接将 LM2596S 的输出线路接 入舵机控制板，则会烧毁我们的舵机控制板，因此需要现行调节 LM2596S 模块的

# 输出电压。 jiaoliuqun:902595482


固定电池：jiaoliuqun:902595482

如下图所示，首先需要将电压调至 5V。接着再给机器人通电，如果通电测 试正常，则可以将机器人电源板固定好。


固定压降模块，注意别让该模块挡住主控板的 micro usb 口，我这里就挡住 了口，不方便烧录代码了。


固定主板：

4.舵机接线

接线的话，按照如下图所示进行接线即可。就是右腿第一个舵机接到板子的 第一个口上面，注意有的板子是从 0 开始有的板子是从 1 号开始，如果板子上面 的舵机标号从 0 开始就从 0 开始接线，如果板子上面的舵机标号从 1 开始就从 1


开始接线。

# jiaoliuqun:902595482

四.Baize_H1mini 机器人代码烧录调试

1.Arduino IDE 配置 ESP8266 开发板

这一步主要是在arduino ide里面添加esp8266的硬件支持，我们默认安装完arduino之后， arduino 里的开发板选项是没有 esp8266 的，因此需要添加硬件支持，让 arduino ide 可以 支持 esp8266 开发板。首先打开 Arduino IDE，点击文件——首选项

jiaoliuqun:902595482

接下来会跳出下方界面，点击箭头 1 所示的那个白色小方框，接着会跳出箭头 2 所示的小窗 口，将该网址——http://arduino.esp8266.com/stable/package_esp8266com_index.json，复制 粘贴到小窗口里面，如图 3 所示，保证这个网址在里面就可以了，然后点击箭头 4 所示的好 即可。


接下来，点击 Arduino IDE 上方的工具——开发板——开发板管理器

接着会跳出来如下窗口，在箭头 1 所示的窗口中输入 esp8266 并敲下回车按钮进行开发板搜 索，接着将会出现图中的 esp8266 选项，点击箭头 2 所示的版本选择最新的版本，根据箭头 3 点击安装即可开始安装，等待进度条完成安装即可。

# jiaoliuqun:902595482


接着，我们在工具——开发板选项里面，就可以看到 esp8266 开发板了，我们选择如下图所 示的开发板即可。

2.配置库文件

在配置了开发板之后，还需要配置我们项目需要用到的库文件，这样我们的程序代码才能正 常编译烧录。
编译是程序编程机器代码的过程，计算机只能直接理解机器代码，我们编写的程序它是不能 直接理解的，因此我们写的程序都需要进行编译计算机才能理解。 烧录是将编译后的程序从电脑上上传到机器人板子上面的芯片里面的过程，只有将程序上传

# jiaoliuqun:902595482

到机器人的板子上面，程序才能正确执行并且控制机器人运行。 找到如下文件夹：

将其复制到自己电脑的如下文件夹里面：

3.烧录代码

烧录代码前，首先根据如下步骤，一步一步通过文件路径找到我们需要的代 码文件。
首先打开 3.Software 这个文件夹

然后打开 Arduino 主程序这个文件夹

# jiaoliuqun:902595482

接着再打开第一个 Baize_HexapodRobot_Arduino 文件夹

然后找到 Baize_HexapodRobot_Arduino.ino 这个程序文件，找到之后可以 双击直接打开。

打开后的界面如下图所示： jiaoliuqun:902595482

接下来，我们选择开发板类型，然后通过软件的验证功能看程序代码是否有 格式错误。
选择开发板类型如下：


然后点击软件界面的验证按钮，可以看到如图，下面出现编译完成的提示，

说明我们的代码没有问题，并且已经通过了编译。 jiaoliuqun:902595482

接下来，我们将开发板通过 Micro USB 线连接到电脑上。
注意：当通过 Micro USB 线连接开发板和电脑时，开发板上不能连接任何舵 机，否则可能烧坏电脑主板。

接下来，点击上传按钮，即可把程序上传到开发板上面。 jiaoliuqun:902595482

五.Baize_H1mini 机器人手机 APP 遥控配置

在测试前，首先需要给你的手机安装一个遥控软件并且进行相应的设置，我 们这里安装的遥控软件名字是 NeTorch，如果你的应用市场可以直接搜到的话， 可以直接在应用市场进行安装。

如果应用市场搜索不到的话，可以将这个软件安装包发送到自己的安卓手机 上，然后再进行安装。
软件安装包位置如下图所示，首先找到 4.Android app 这个文件夹。

如下图所示的 NeTorch.apk 就是我们需要找到的手机遥控软件安装包，你可 以通过 QQ 或者微信将安装包发送到手机上进行安装。

安装之后打开如下图所示：


接下来，需要你用自己的手机开个热点。
热点名字(SSID)是：Baize
热点密码(PASS)是：baizerobot
接下来需要给机器人通电，机器人通电之后，可看到主板上有个蓝灯亮起来 了。
如果蓝灯过几秒之后变为闪烁状态，则代表着机器人主板已经连接到了手机 热点，网络连接正常。
接下来可以设置手机遥控 APP 进行遥控了。
首先需要你查看一下机器人的 IP 地址，点击个人热点之后，可以看到有一 个设备连接了你的手机，这里可以看到如下图所示界面，我们可以看到这个 IP

地址为：192.168.43.227，这里需要你先记下这个 IP 地址。 jiaoliuqun:902595482


然后打开 Netorch 软件界面，进行相应的设置：

然后我们设置按钮：
首先点击按钮模式，接下来长按按钮就可以进行按钮的设置了。我们点开按 钮把相应的前后左右设置好，按照如下图完成按钮的设置。

# jiaoliuqun:902595482


控制指令表如下：
控制指令表
指令 | 动作 | 指令 | 动作
a | 前进行走 | f | 向左横移
b | 后退行走 | g | 向右横移
c | 原地左转 | h | 步态切换
d | 原地右转 | i | 身高切换
e | 停止

后续会更新更多动作指令！

# jiaoliuqun:902595482

接下来便可以进行遥控操作测试了，点击一下前进的按钮，是不是已经发现 机器人开始前进了呢？
接下来可以愉快的玩耍了。

# jiaoliuqun:902595482

### 六.白泽舵机驱动板 (https://blog.csdn.net/qqliuzhitong/article/details/124497060)

这是一块 32 路舵机驱动板，做舵机机器人非常方便。主控用的 esp8266。 电源用的 5V 的电池，电池直接给舵机供电，经过压降之后产生 3.3V 电压给 esp8266 模组供电。
这块板儿主要是用于控制 sg90 舵机，就是那种蓝色舵机，或者 mg90s 舵机。 后续会升级，升级后可以控制 5-12V 的 pwm 舵机。 这样就可以控制高压的舵机，比如型号为 mg996r 或 mg995 的舵机。 3D 图片如下图所示：

实物图如下：jiaoliuqun:902595482

测试代码：

例程 1：控制 32 路舵机匀速旋转从 0-180 度

/*******************************************************
主板：Baize_ServoDriver_esp8266 | 开源链接：
https://github.com/Allen953/Baize_ServoDriver_esp8266 功能：控制 32 路舵机匀速旋转从 0-180 度
引脚：SDA:21 SCL:22
Designer: Allen
E-mail:953598974@qq.com
Date:2022-08-24
*******************************************************/

#include <Wire.h>

#include <Adafruit_PWMServoDriver.h>

Adafruit_PWMServoDriver pwm = Adafruit_PWMServoDriver(); Adafruit_PWMServoDriver pwm1 = Adafruit_PWMServoDriver(0x41);

#define SERVOMIN 102 | //0.5/20 * 4096 = 102

#define SERVOMAX 512 | //2.5/20 * 4096 = 512

void setup() {
Serial.begin(115200);
Serial.println();
Serial.println("16 channel Servo test!");

pwm.begin();
pwm1.begin();
pwm.setPWMFreq(50); // Analog servos run at ~50 Hz updates pwm1.setPWMFreq(50); // Analog servos run at ~50 Hz updates

delay(200);
for(int i=0;i<16;i++)
{
pwm.setPWM(i, 0, SERVOMIN); // 驱动 32 路舵机转到 0 度 pwm1.setPWM(i, 0, SERVOMIN);// 驱动 32 路舵机转到 0 度

# jiaoliuqun:902595482

}
delay(2000);
for (uint16_t pulselen = SERVOMIN; pulselen < SERVOMAX; pulselen++) { for(int i=0;i<16;i++)
{
pwm.setPWM(i, 0, pulselen); pwm1.setPWM(i, 0, pulselen);
}
delayMicroseconds(200);
ESP.wdtFeed(); | //喂狗防止复位
}
}

void loop() {

}

例程 2：控制 32 路舵机匀速旋转从 0-180 度，再从 180-0 度

/*******************************************************
主板：Baize_ServoDriver_esp8266 | 开源链接：
https://github.com/Allen953/Baize_ServoDriver_esp8266 功能：控制 32 路舵机匀速旋转从 0-180 度，再从 180-0 度 引脚：SDA:21 SCL:22
Designer: Allen
E-mail:953598974@qq.com
Date:2022-08-24
*******************************************************/

#include <Wire.h>

#include <Adafruit_PWMServoDriver.h>

Adafruit_PWMServoDriver pwm = Adafruit_PWMServoDriver(); Adafruit_PWMServoDriver pwm1 = Adafruit_PWMServoDriver(0x41);

#define SERVOMIN 102 | //0.5/20 * 4096 = 102

#define SERVOMAX 512 | //2.5/20 * 4096 = 512

void setup() {
Serial.begin(115200);
Serial.println("16 channel Servo test!");

# jiaoliuqun:902595482

pwm.begin();
pwm1.begin();
pwm.setPWMFreq(50); // Analog servos run at ~50 Hz updates pwm1.setPWMFreq(50); // Analog servos run at ~50 Hz updates }

void loop() {
for (uint16_t pulselen = SERVOMIN; pulselen < SERVOMAX; pulselen++) {
for(int i=0;i<16;i++)
{
pwm.setPWM(i, 0, pulselen); pwm1.setPWM(i, 0, pulselen);
}
delayMicroseconds(200);
ESP.wdtFeed(); | //喂狗防止复位
}
for (uint16_t pulselen = SERVOMAX; pulselen > SERVOMIN; pulselen--) {
for(int i=0;i<16;i++)
{
pwm.setPWM(i, 0, pulselen); pwm1.setPWM(i, 0, pulselen);
}
delayMicroseconds(200);
ESP.wdtFeed(); | //喂狗防止复位
}
}

例程 3：控制 32 路舵机从 0，90，180，90，0 度之间循环。

/*******************************************************
主板：Baize_ServoDriver_esp8266 | 开源链接：
https://github.com/Allen953/Baize_ServoDriver_esp8266 功能：控制 32 路舵机从 0，90，180，90，0 度之间循环 引脚：SDA:21 SCL:22
Designer: Allen
E-mail:953598974@qq.com
Date:2022-08-24
*******************************************************/

#include <Wire.h>

# jiaoliuqun:902595482

#include <Adafruit_PWMServoDriver.h>

Adafruit_PWMServoDriver pwm = Adafruit_PWMServoDriver(); Adafruit_PWMServoDriver pwm1 = Adafruit_PWMServoDriver(0x41);

#define SERVOMIN 102 | //0.5/20 * 4096 = 102

#define SERVOMID 307 | //(102+512)/2=307

#define SERVOMAX 512 | //2.5/20 * 4096 = 512

//pwm.setPWM(i, 0, pulse);i=0~15 对应第 0-15 个舵机；pwm1.setPWM(j, 0, pulse);j=0~15 对应第 16-31 个舵机，

void setup() {
Serial.begin(115200);
Serial.println("16 channel Servo test!");

pwm.begin();
pwm1.begin();
pwm.setPWMFreq(50); // Analog servos run at ~50 Hz updates pwm1.setPWMFreq(50); // Analog servos run at ~50 Hz updates }

void loop() {
//全部舵机转到 0 度
for(int i=0;i<16;i++)
{
pwm.setPWM(i, 0, SERVOMIN); pwm1.setPWM(i, 0, SERVOMIN);
}
delayMicroseconds(200);
ESP.wdtFeed(); | //喂狗防止复位
delay(1000);
//全部舵机转到 90 度
for(int i=0;i<16;i++)
{
pwm.setPWM(i, 0, SERVOMID); pwm1.setPWM(i, 0, SERVOMID);
}
delayMicroseconds(200);
ESP.wdtFeed(); | //喂狗防止复位
delay(1000);
//全部舵机转到 180 度
for(int i=0;i<16;i++)
{

# jiaoliuqun:902595482

pwm.setPWM(i, 0, SERVOMAX); pwm1.setPWM(i, 0, SERVOMAX);
}
delayMicroseconds(200);
ESP.wdtFeed(); | //喂狗防止复位
delay(1000);
//全部舵机转到 90 度
for(int i=0;i<16;i++)
{
pwm.setPWM(i, 0, SERVOMID); pwm1.setPWM(i, 0, SERVOMID);
}
delayMicroseconds(200);
ESP.wdtFeed(); | //喂狗防止复位
delay(1000);
}

例程 4：板子连到手机热点

手机需要开一个热点，名字："Baize"，密码："baizerobot"。

然后上传这个程序到板子上，在手机上就能看到板子连到手机热点了。

//修改自：
https://blog.csdn.net/wangke0809/article/details/70146378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 nk_v2_pc_rank_v29&utm_term=esp8266%E4%B8%B2%E5%8F%A3%E9%80%8F%E4%BC%A 0%E7%A8%8B%E5%BA%8F&spm=1018.2226.3001.4187
//原作者：wangke0809
#include <ESP8266WiFi.h>

#define MAX_SRV_CLIENTS 3 //最大同时联接数，即你想要接入的设备数量， 8266tcpserver 只能接入五个，哎

const char *ssid = "Baize";
const char *password = "baizerobot";

WiFiServer server(8266);//你要的端口号，随意修改，范围 0-65535 WiFiClient serverClients[MAX_SRV_CLIENTS];

void setup()

# jiaoliuqun:902595482

{
Serial.begin(9600);
delay(10);
pinMode(16, OUTPUT);
digitalWrite(16, 0);
WiFi.begin(ssid, password);

while (WiFi.status() != WL_CONNECTED) {
delay(500);
}
server.begin();
server.setNoDelay(true); //加上后才正常些 }

void loop()
{
blink();

uint8_t i;
if (server.hasClient())
{
for (i = 0; i < MAX_SRV_CLIENTS; i++)
{
if (!serverClients[i] || !serverClients[i].connected())
{
if (serverClients[i]) serverClients[i].stop();//未联接, 就释放
serverClients[i] = server.available();//分配新的 continue;
}

}
WiFiClient serverClient = server.available(); serverClient.stop();
}
for (i = 0; i < MAX_SRV_CLIENTS; i++)
{
if (serverClients[i] && serverClients[i].connected()) {
digitalWrite(16, 0);//有链接存在,就一直长亮

if (serverClients[i].available())
{

# jiaoliuqun:902595482

while (serverClients[i].available()) Serial.write(serverClients[i].read()); }
}
}
if (Serial.available())
{
size_t len = Serial.available();
uint8_t sbuf[len];
Serial.readBytes(sbuf, len);
//push UART data to all connected telnet clients
for (i = 0; i < MAX_SRV_CLIENTS; i++)
{
if (serverClients[i] && serverClients[i].connected())
{
serverClients[i].write(sbuf, len); //向所有客户端发 送数据
delay(1);
}
}
}
}

void blink()
{
static long previousMillis = 0;
static int currstate = 0;

if (millis() - previousMillis > 200) //200ms {
previousMillis = millis();
currstate = 1 - currstate; digitalWrite(16, currstate); }
}

例程 5：发现（校验）板子上的 iic 设备

/*******************************************************
主板：Baize_ServoDriver_esp8266 | 开源链接：
https://github.com/Allen953/Baize_ServoDriver_esp8266

# jiaoliuqun:902595482

功能：扫描 IIC 总线上挂载的设备
引脚：SDA:21 SCL:22
Designer: Allen
E-mail:953598974@qq.com
Date:2022-08-24
*******************************************************/

#include <Wire.h>

void setup()
{
Wire.begin();
Serial.begin(115200);
}

void loop()
{
byte error, address;
int nDevices;
Serial.println();
Serial.println("Scanning...");

nDevices = 0;
for(address = 1; address < 127; address++ ) {
Wire.beginTransmission(address);
error = Wire.endTransmission();

if (error == 0)
{
Serial.print("I2C device found at address 0x"); if (address<16)
Serial.print("0");
Serial.print(address,HEX);
Serial.println(" !");

nDevices++;
}
else if (error==4)
{
Serial.print("Unknown error at address 0x"); if (address<16)
Serial.print("0");
Serial.println(address,HEX);

# jiaoliuqun:902595482

}
}
if (nDevices == 0)
Serial.println("No I2C devices found\n"); else
Serial.println("done\n");
delay(5000);
}

例程 6：带电压监测的板子测试程序

升级版，主控 esp32。供电范围 5-12V。当我用 7.4V 的 2S 锂电池给舵机供电时， 用这个程序来进行板子测试，由于测试时间较长，担心电池过放，所以通过电压 监测，当电压过低时，将不再驱动舵机工作。

/***************************************************
对于 ARDUINO UNO，这时 SCL->A5，SDA - >A4
对于 ESP8266，这时 SCL->GPIO5，SDA - >GPIO4 ****************************************************/

#include <Wire.h>

#include <Adafruit_PWMServoDriver.h>

Adafruit_PWMServoDriver pwm = Adafruit_PWMServoDriver(); Adafruit_PWMServoDriver pwm1 = Adafruit_PWMServoDriver(0x41);

#define SERVOMIN 102 | //0.5/20 * 4096 = 102

#define SERVOMAX 512 | //2.5/20 * 4096 = 512

//pcb 板测试时，如果是 2S 的锂电池供电，则以此电压为阈值，低于此电压时， 不再驱动舵机运动，保护电池。
float voltage_threshold = 6.5;
int voltage_testpin = 26;
float voltage_b = 0.0;

bool servo_f = 1;

void setup() {
Serial.begin(115200);
Serial.println();

# jiaoliuqun:902595482

Serial.println("16 channel Servo test!");

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

delay(200);
for(int i=0;i<16;i++)
{
pwm.setPWM(i, 0, SERVOMIN); // 驱动 32 路舵机转到 0 度 pwm1.setPWM(i, 0, SERVOMIN);// 驱动 32 路舵机转到 0 度
}
delay(2000);
for (uint16_t pulselen = SERVOMIN; pulselen < SERVOMAX; pulselen++) { for(int i=0;i<16;i++)
{
pwm.setPWM(i, 0, pulselen); pwm1.setPWM(i, 0, pulselen); }
delayMicroseconds(200);
}
}

void loop() {
if(servo_f==1)
{
for (uint16_t pulselen = SERVOMIN; pulselen < SERVOMAX; pulselen++) {
for(int i=0;i<16;i++)
{
pwm.setPWM(i, 0, pulselen); pwm1.setPWM(i, 0, pulselen); }
delayMicroseconds(200);
}
//电压检测
int voltage_sum = 0.0;
for(int i=0;i<10;i++)
{
voltage_sum +=
float(analogRead(voltage_testpin))/4095.0*3.3*4.0; Serial.println(analogRead(voltage_testpin)); delay(100);

# jiaoliuqun:902595482

}
voltage_b = voltage_sum / 10.0; Serial.println(voltage_b); if(voltage_b<voltage_threshold) servo_f = 0;

for(int i=0;i<16;i++)
{
pwm.setPWM(i, 0, SERVOMIN); // 驱动 32 路舵机转到 0 度 pwm1.setPWM(i, 0, SERVOMIN);// 驱动 32 路舵机转到 0 度 }
delay(2000);
}

}

例程 7：串口控制舵机角度

/*******************************************************
主板：Baize_ServoDriver_esp8266 | 开源链接：
https://github.com/Allen953/Baize_ServoDriver_esp8266 功能：串口输入角度，板子驱动舵机转到该角度
引脚：SDA:21 SCL:22
Designer: Allen
E-mail:953598974@qq.com
Date:2022-08-24
*******************************************************/ #include <Wire.h>
#include <Adafruit_PWMServoDriver.h>

Adafruit_PWMServoDriver pwm = Adafruit_PWMServoDriver(); //驱动 1~16 或(0~15)号舵机
Adafruit_PWMServoDriver pwm1 = Adafruit_PWMServoDriver(0x41); //驱动 17~32 或(16~31)号舵机
//#define SERVOMIN 102 | //0.5/20 * 4096 = 102
//#define SERVOMID 307 | //1.5/20 * 4096 = 307
//#define SERVOMAX 512 | //2.5/20 * 4096 = 512
//实际测试
#define SERVOMIN 102

#define SERVOMID 327

# jiaoliuqun:902595482

#define SERVOMAX 552

void setup() {
// put your setup code here, to run once: Serial.begin(115200);

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

}

void loop() {
// put your main code here, to run repeatedly: while(!(Serial.available()>0))ESP.wdtFeed();//喂狗防止复位 int pwmsum=Serial.parseInt();

for(int i=0;i<16;i++)
{
pwm.setPWM(i, 0, pwmsum);
}
pwm1.setPWM(0, 0, pwmsum); pwm1.setPWM(1, 0, pwmsum); delay(100);
}

固件烧录

有些小伙伴没有安装好 arduino ide 或者没有安装好 esp8266 的硬件支持包，这 个时候呢，就没法编译程序进行烧录了。

所以我在资料文件夹里面放上了编译好的固件，咱们就无需编译直接使用烧录工 具就可以把固件给烧录到板子上了。

找到烧录工具并打开

# jiaoliuqun:902595482

编辑

打开烧录程序

编辑

选中 com 口

# jiaoliuqun:902595482

编辑

点击齿轮选中要烧录的固件(.bin 格式)，填写烧录地址，并在要烧录的固件前 面打勾。

编辑

选择上传的波特率，flash 大小，flash 速度等。

然后点击 flash 进行烧录，烧录完成后，进度条会跑满，左下角会出现绿色打勾 符号。

# jiaoliuqun:902595482

按一下板子上的 rst 按键，重启板子，程序就开始执行了。

我遇到的问题

1.插电脑不出 com 口，怎么操作都没用

ch340 芯片焊错了，焊成了 ch340g 芯片，导致 usb-ttl 芯片无法正常工作。

2.插电脑不出 com 口，按住 rst 按键会出 com 口，松开又消失

原因是台式机电脑前面的 usb 口能供应的电流太小了，带不起来板子。

当按住 rst 的时候，esp8266 模组这个时候相当于是关机了，esp8266 模组不工 作的时候，整个板子自然功耗下降下来，然后 ch340c 芯片工作正常，这样一来 电脑就出 com 口了。

而一旦松开 rst，这个时候 esp8266 模组要开始工作，板子功耗又起来了，usb

口带不动过载了，所以 ch340c 芯片无法正常工作，com 口就消失了。 jiaoliuqun:902595482

七 3D (https://blog.csdn.net/qqliuzhitong/article/details/116492164) 打印开源六足机器人程序 (https://blog.csdn.net/qqliuzhitong/article/details/116492164)

3.编程例程

持续更新中！！！！！！！

# jiaoliuqun:902595482

附录

# jiaoliuqun:902595482

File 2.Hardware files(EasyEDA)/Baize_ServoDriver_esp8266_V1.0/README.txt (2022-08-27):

<p>该舵机驱动板可以同时驱动32个sg90或者mg90s小型舵机。</p>
<p>只要是电压在5V的pwm舵机都可以驱动。</p>
<p>项目可以自由复制，分享。</p>
<p>如果将其用于商业用途，可以直接用。</p>            
How to use：

At editor, open the document via: Top menu - File - Open - EasyEDA... , and select the json file, then open it at the editor, you can save it into a project.

如何使用：

打开编辑器，通过：顶部菜单 - 文件 - 打开 - 立创EDA... ，选择 json 文件打开在编辑器，你可以保存文档进工程里面。

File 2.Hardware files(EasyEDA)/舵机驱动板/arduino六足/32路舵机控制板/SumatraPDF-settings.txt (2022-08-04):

# For documentation, see http://www.sumatrapdfreader.org/settings3.1.html

MainWindowBackground = #80fff200
EscToExit = false
ReuseInstance = false
UseSysColors = false
RestoreSession = auto

FixedPageUI [
	TextColor = #000000
	BackgroundColor = #ffffff
	SelectionColor = #f5fc0c
	WindowMargin = 2 4 2 4
	PageSpacing = 4 4
]
EbookUI [
	FontName = Georgia
	FontSize = 12.5
	TextColor = #5f4b32
	BackgroundColor = #fbf0d9
	UseFixedPageUI = false
]
ComicBookUI [
	WindowMargin = 0 0 0 0
	PageSpacing = 4 4
	CbxMangaMode = false
]
ChmUI [
	UseFixedPageUI = false
]
ExternalViewers [
]
PrereleaseSettings [
	TabWidth = 300
]
ShowMenubar = true
ReloadModifiedDocuments = true
FullPathInTitle = false
ZoomLevels = 8.33 12.5 18 25 33.33 50 66.67 75 100 125 150 200 300 400 600 800 1000 1200 1600 2000 2400 3200 4800 6400
ZoomIncrement = 0

PrinterDefaults [
	PrintScale = shrink
]
ForwardSearch [
	HighlightOffset = 0
	HighlightWidth = 15
	HighlightColor = #6581ff
	HighlightPermanent = false
]
AnnotationDefaults [
	HighlightColor = #ffff60
	SaveIntoDocument = true
]
CustomScreenDPI = 0

RememberStatePerDocument = true
UiLanguage = cn
ShowToolbar = true
ShowFavorites = false
AssociateSilently = false
CheckForUpdates = true
RememberOpenedFiles = true
EnableTeXEnhancements = false
DefaultDisplayMode = automatic
DefaultZoom = fit page
WindowState = 1
WindowPos = 562 0 795 1030
ShowToc = true
SidebarDx = 0
TocDy = 0
ShowStartPage = true
UseTabs = true

FileStates [
]
SessionData [
]
TimeOfLastUpdateCheck = 0 0
OpenCountWeek = 538

# Settings after this line have not been recognized by the current version

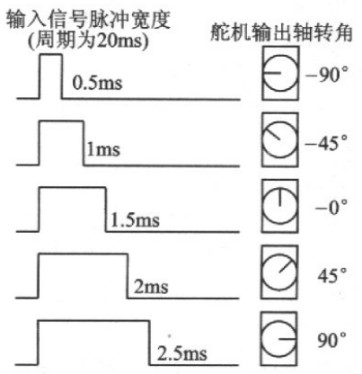
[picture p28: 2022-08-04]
2.Hardware files(EasyEDA)/舵机驱动板/arduino六足/mg996r舵机/TB273zKDAKWBuNjy1zjXXcOypXa_!!361121710.jpg

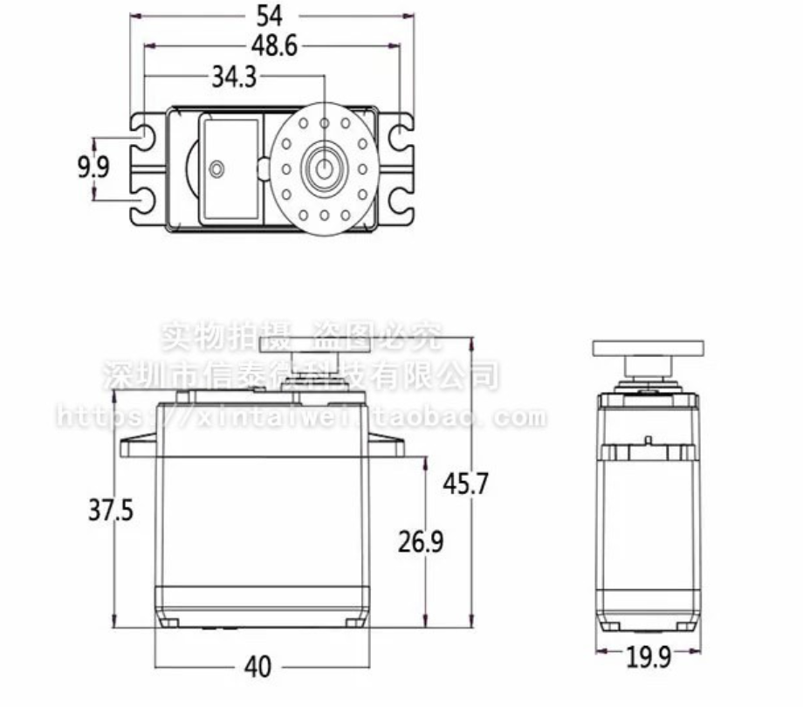
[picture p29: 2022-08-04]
2.Hardware files(EasyEDA)/舵机驱动板/arduino六足/mg996r舵机/QQ[G}Z$5[ZFQRTJNOQQ@BF7.png

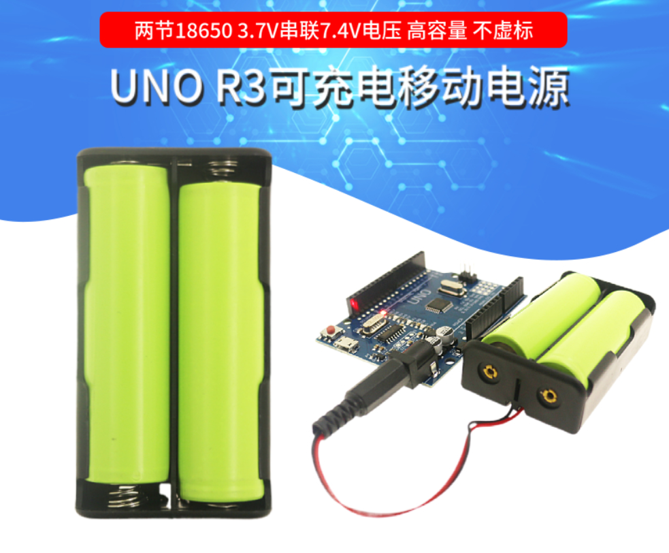
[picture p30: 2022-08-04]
2.Hardware files(EasyEDA)/舵机驱动板/arduino六足/arduino电源参数.png

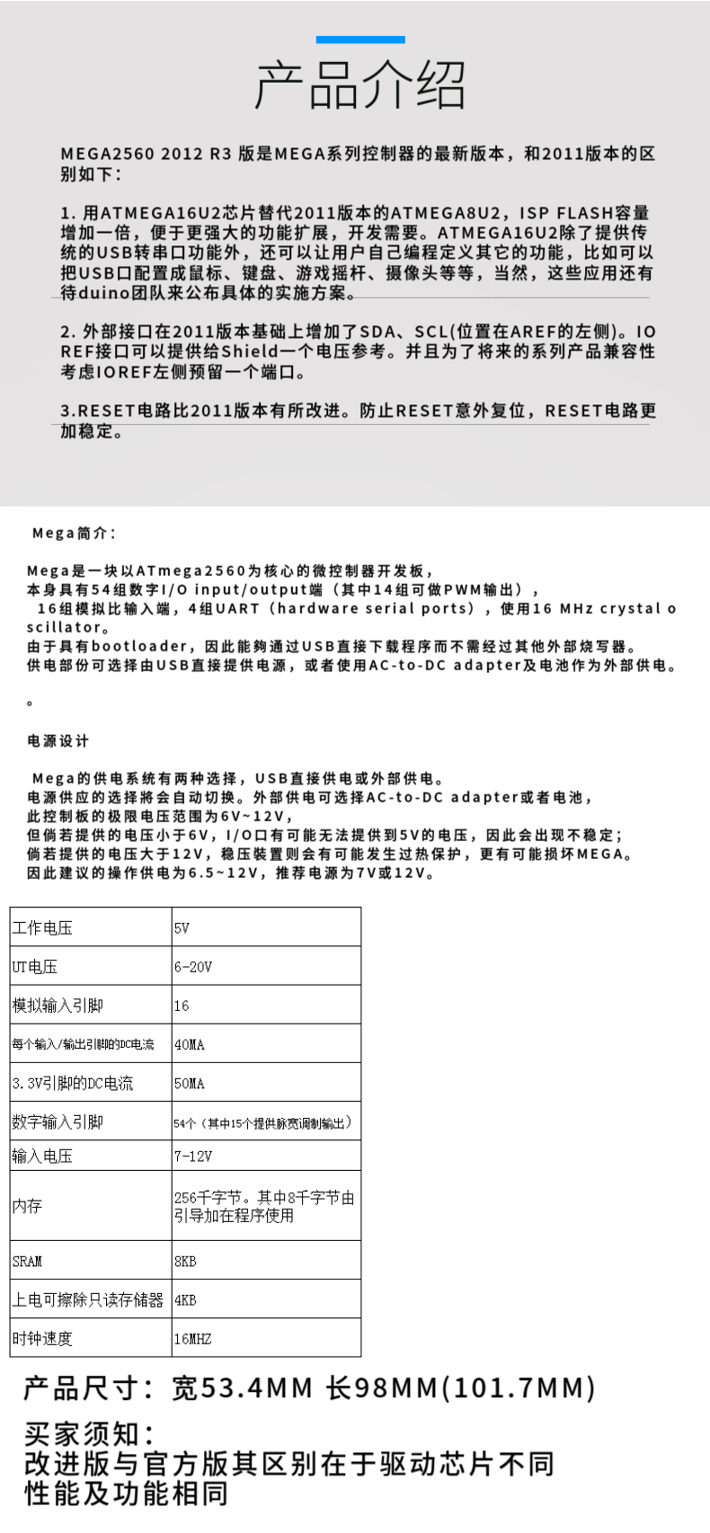
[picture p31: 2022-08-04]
2.Hardware files(EasyEDA)/舵机驱动板/arduino六足/mega2560r3官方/参数.png

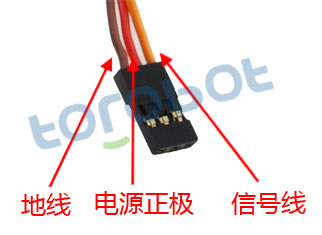
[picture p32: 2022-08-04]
2.Hardware files(EasyEDA)/舵机驱动板/arduino六足/32路舵机控制板/舵机的三根线.jpg

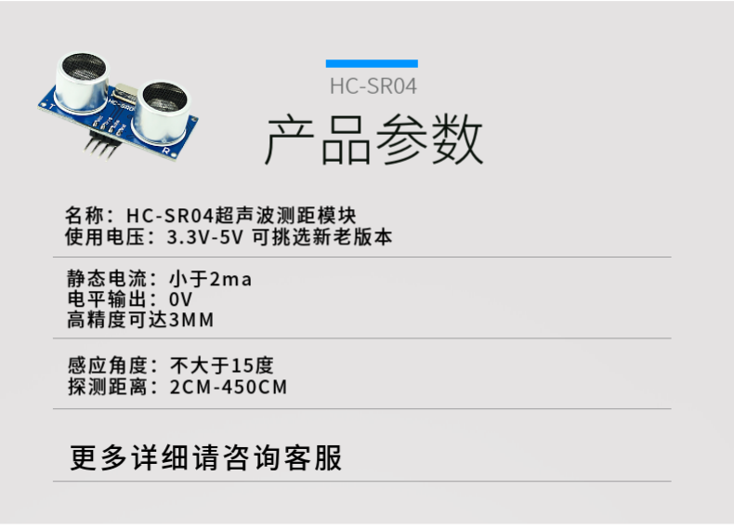
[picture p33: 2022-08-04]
2.Hardware files(EasyEDA)/舵机驱动板/arduino六足/超声波模块参数.png

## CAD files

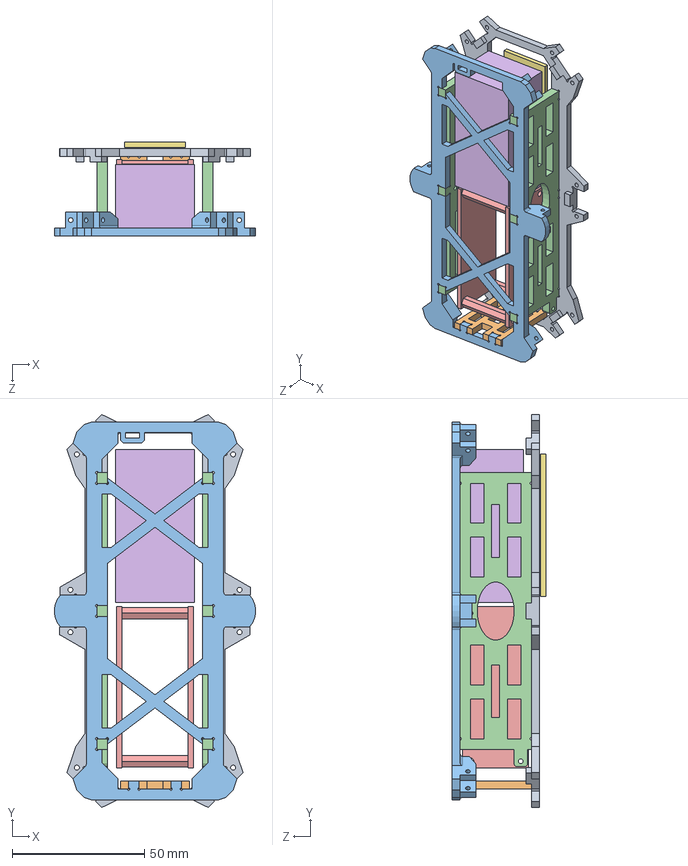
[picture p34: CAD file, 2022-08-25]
1.3D model/Baize_HexapodRobot_Arduino_3DPrinter/body.SLDASM
76.2 x 148.7 x 35.5 mm
body_top
body_back_wall
body_bottom
body_side_wall x 2
驱动板
电池
变压

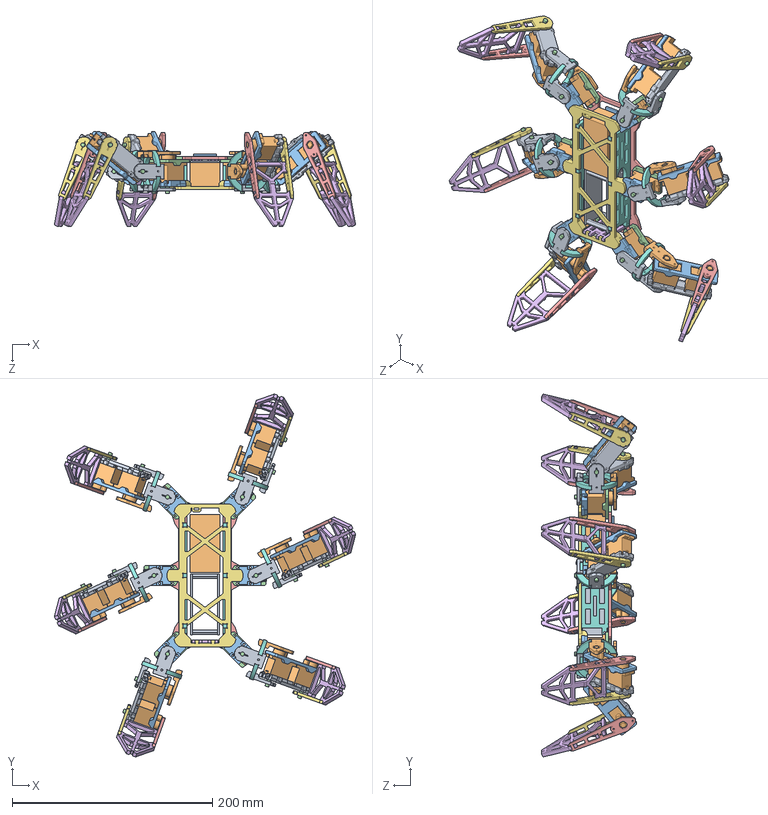
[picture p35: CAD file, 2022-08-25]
1.3D model/Baize_HexapodRobot_Arduino_3DPrinter/总装.SLDASM
300.9 x 362.5 x 95.0 mm
leg_bottom x 6
MG90S x 18
leg_top x 6
销轴4x10 x 18
foot_top x 6
foot_ground x 6
foot_bottom x 6
joint_cross x 6
joint_bottom x 12
joint_top x 12
thigh_bottom x 6
thigh_top x 6
body_top
body_back_wall
body_bottom
body_side_wall x 2
驱动板
电池
变压

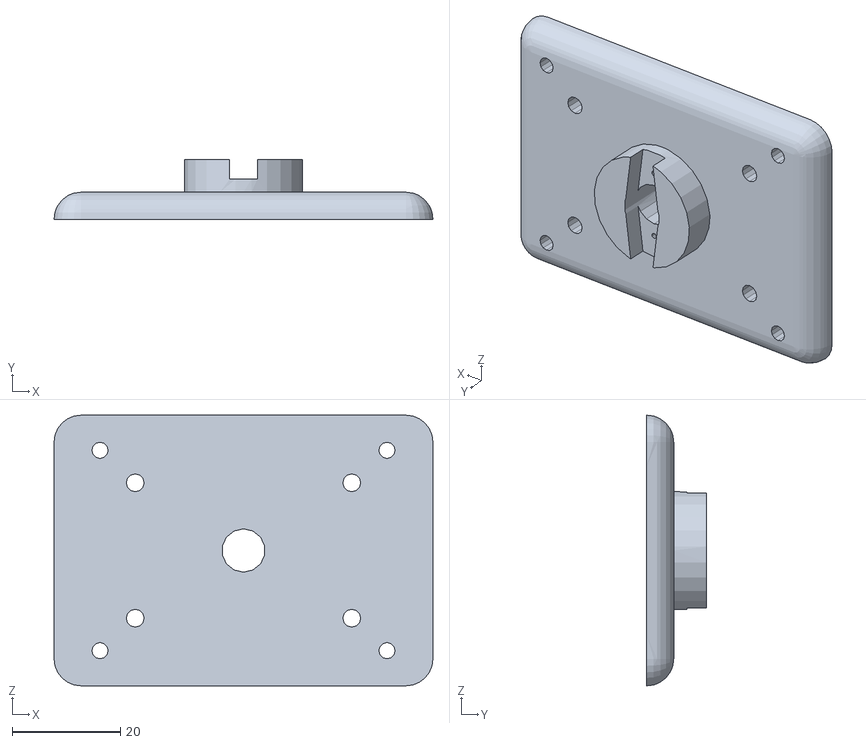
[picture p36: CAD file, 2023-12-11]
1.3D model/PTZbase.STL
70.0 x 11.0 x 50.0

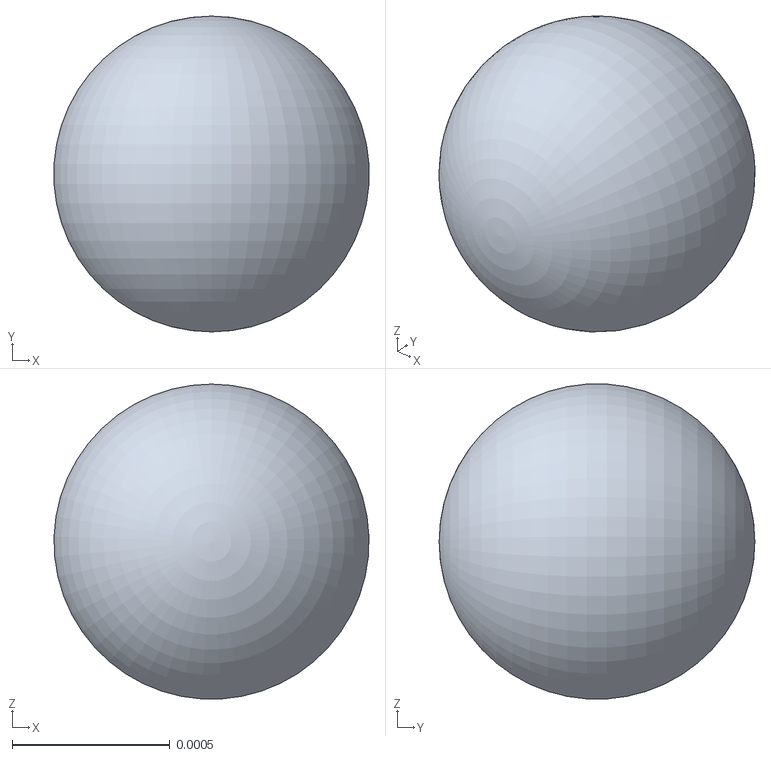
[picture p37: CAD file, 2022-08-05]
3.Software/ROS_package/Urdf_ConfigFiles/meshes/RB_Y_LINK.STL
0.000998 x 0.001 x 0.000997

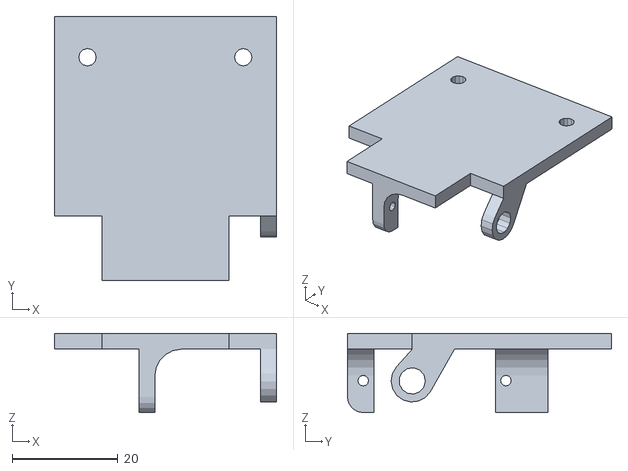
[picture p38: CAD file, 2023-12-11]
1.3D model/head.STL
42.0 x 50.0 x 15.0

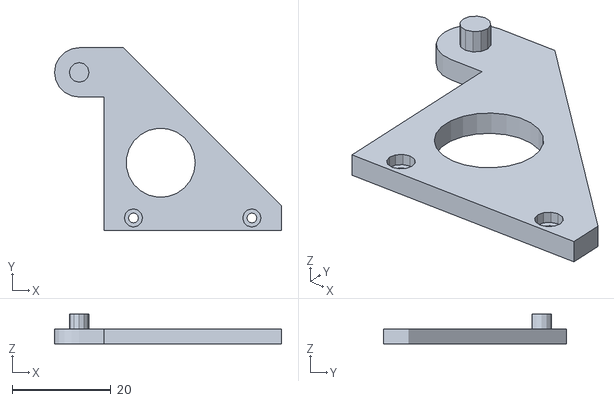
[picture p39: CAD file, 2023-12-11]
1.3D model/PTZleft.STL
46.0 x 37.0 x 6.00

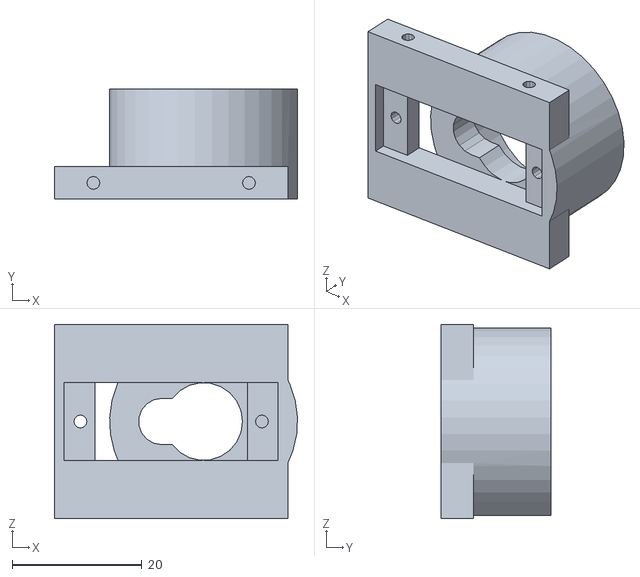
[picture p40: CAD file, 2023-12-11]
1.3D model/rotate.STL
37.5 x 17.0 x 30.0

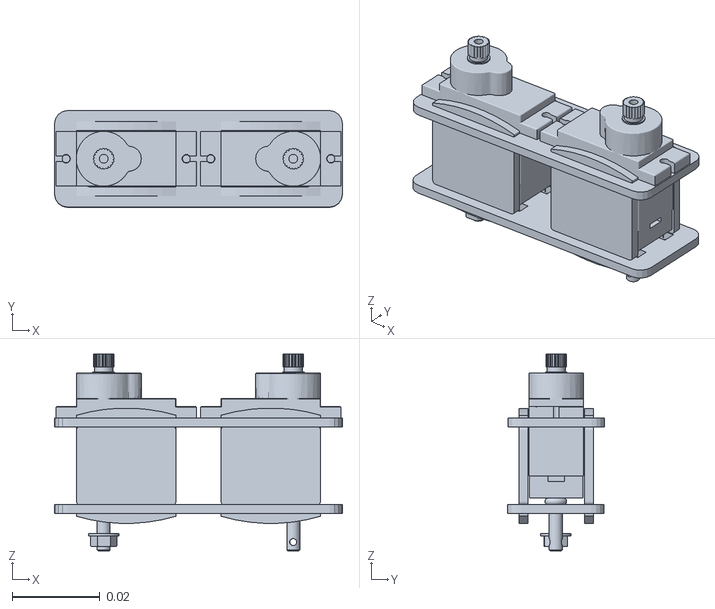
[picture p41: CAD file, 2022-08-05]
3.Software/ROS_package/Urdf_ConfigFiles/meshes/RM_ZHOU_LINK.STL
0.0656 x 0.0221 x 0.0448

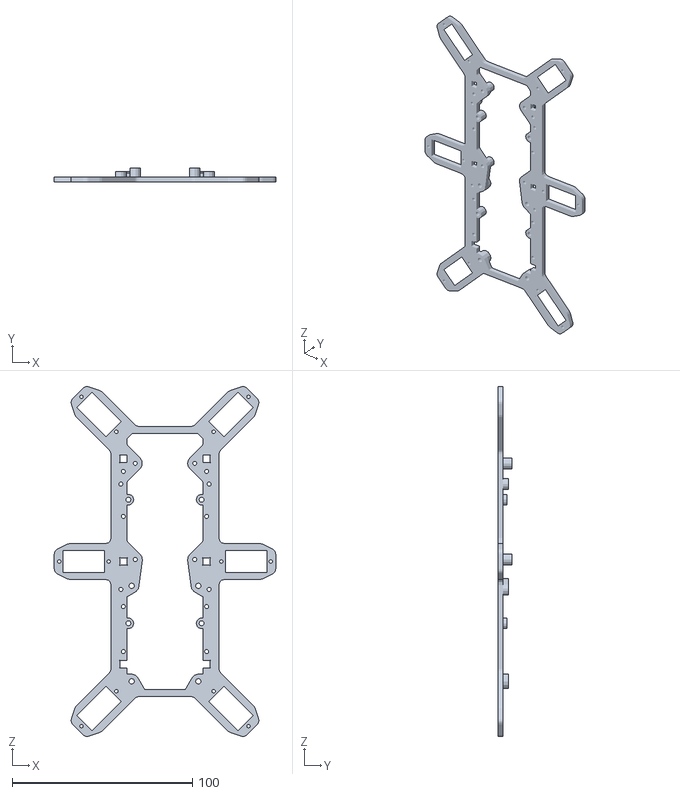
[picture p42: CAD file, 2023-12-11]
1.3D model/body_top1.STL
123.0 x 8.00 x 194.3

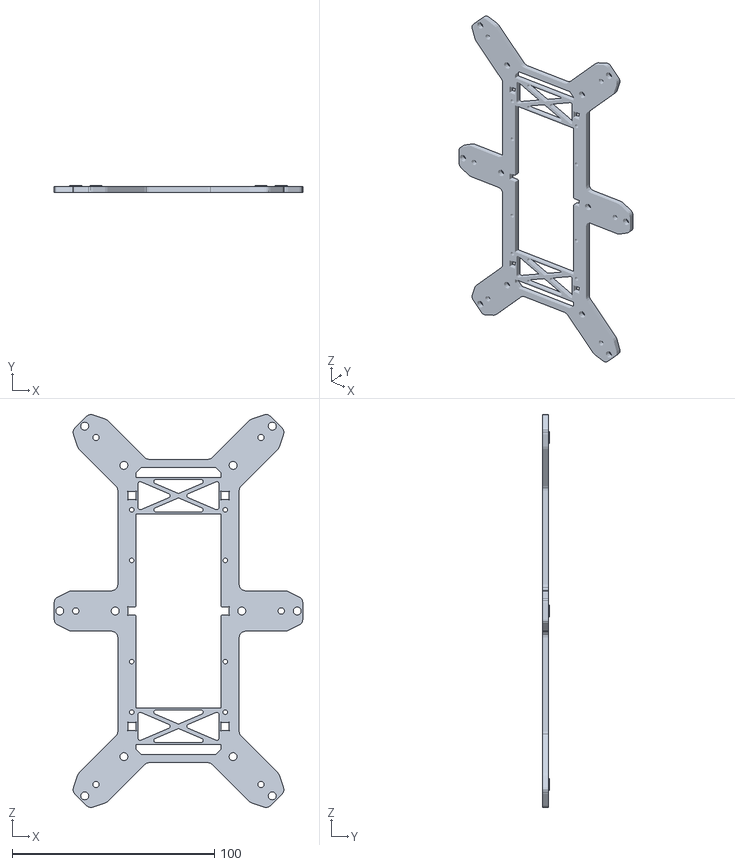
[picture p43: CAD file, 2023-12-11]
1.3D model/body_bottom1.STL
123.0 x 3.50 x 194.3

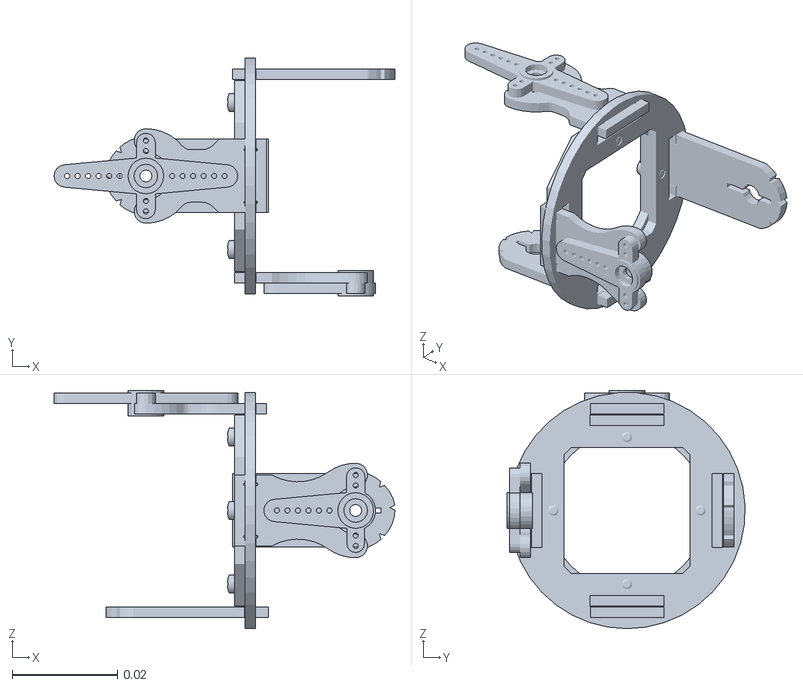
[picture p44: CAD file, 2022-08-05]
3.Software/ROS_package/Urdf_ConfigFiles/meshes/LM_JIAN_LINK.STL
0.0649 x 0.0454 x 0.0454

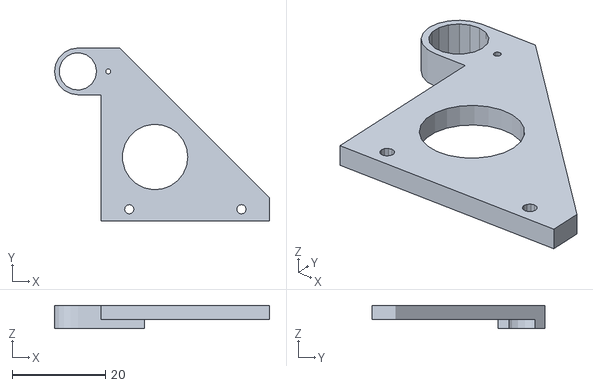
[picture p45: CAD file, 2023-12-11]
1.3D model/right.STL
46.0 x 37.0 x 5.00

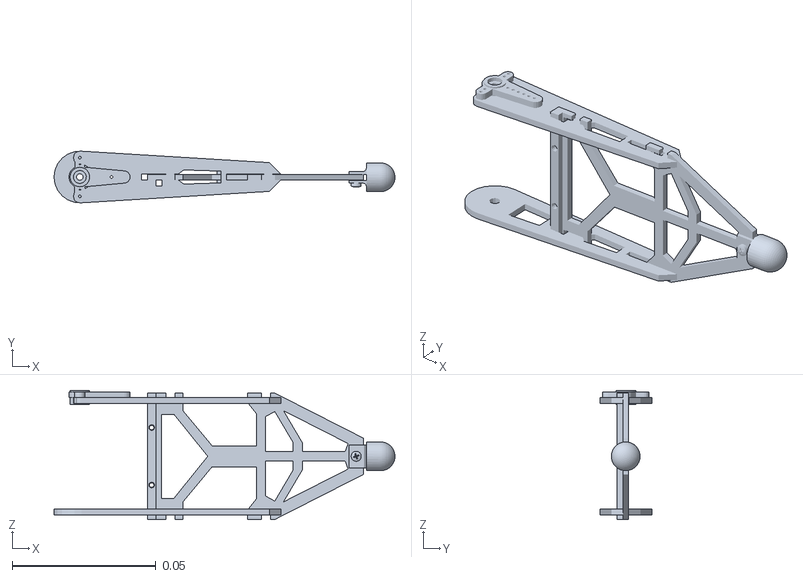
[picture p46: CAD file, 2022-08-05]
3.Software/ROS_package/Urdf_ConfigFiles/meshes/RB_XI_LINK.STL
0.119 x 0.018 x 0.0449

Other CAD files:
3.Software/ROS_package/Urdf_ConfigFiles/meshes/LM_R_LINK.STL
3.Software/ROS_package/Urdf_ConfigFiles/meshes/LF_R_LINK.STL
3.Software/ROS_package/Urdf_ConfigFiles/meshes/LM_ZHOU_LINK.STL
3.Software/ROS_package/Urdf_ConfigFiles/meshes/LB_R_LINK.STL
1.3D model/PTZhead.STL
1.3D model/body_mid1.STL
1.3D model/body_side_wall2.STL
1.3D model/foot_bottom_6.STL
1.3D model/foot_ground_6.STL
1.3D model/foot_top_6.STL
1.3D model/joint_bottom_12.STL
1.3D model/joint_cross_6.STL
1.3D model/joint_top12.STL
1.3D model/leg_bottom6.STL
1.3D model/leg_top_6.STL
3.Software/ROS_package/Urdf_ConfigFiles/meshes/LB_JIAN_LINK.STL
3.Software/ROS_package/Urdf_ConfigFiles/meshes/LB_P_LINK.STL
3.Software/ROS_package/Urdf_ConfigFiles/meshes/LB_XI_LINK.STL
3.Software/ROS_package/Urdf_ConfigFiles/meshes/LB_ZHOU_LINK.STL
3.Software/ROS_package/Urdf_ConfigFiles/meshes/LF_JIAN_LINK.STL
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

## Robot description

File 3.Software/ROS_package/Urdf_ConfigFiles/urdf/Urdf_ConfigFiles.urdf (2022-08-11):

<?xml version="1.0" encoding="utf-8"?>
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
<robot name="Urdf_ConfigFiles">
  <link name="base_link">
    <inertial>
      <origin xyz="-0.00495925277676378 -3.90134842870204E-05 0.00279738369756694" rpy="0 0 0" />
      <mass value="0.118532698310348" />
      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
    </inertial>
    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
  </link>
  <link name="RM_JIAN_LINK">
    <inertial>
      <origin xyz="0.0187543594677149 -0.000379261050061135 0.000812950598078848" rpy="0 0 0" />
      <mass value="0.00699822854338534" />
      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
    </inertial>
    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
  </link>
  <joint name="RM_JIAN_JOINT" type="revolute">
    <origin xyz="0 -0.050828 0.0045" rpy="0 0 -1.5708" />
    <parent link="base_link" />
    <child link="RM_JIAN_LINK" />
    <axis xyz="0 0 1" />
    <limit lower="-1.5708" upper="1.5708" effort="0" velocity="0" />
  </joint>
  <link name="RM_ZHOU_LINK">
    <inertial>
      <origin xyz="0.0212109550888898 -1.20022572680017E-05 0.00316734503657168" rpy="0 0 0" />
      <mass value="0.023428071079214" />
      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
    </inertial>
    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
  </link>
  <joint name="RM_ZHOU_JOINT" type="revolute">
    <origin xyz="0.039955 0.0049 0.0001" rpy="1.5708 0 0" />
    <parent link="RM_JIAN_LINK" />
    <child link="RM_ZHOU_LINK" />
    <axis xyz="0 0 1" />
    <limit lower="-1.5708" upper="1.5708" effort="0" velocity="0" />
  </joint>
  <link name="RM_XI_LINK">
    <inertial>
      <origin xyz="0.0466384686418486 -7.84327888617709E-05 0.000588778480515891" rpy="0 0 0" />
      <mass value="0.00724422080433269" />
      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
    </inertial>
    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
  </link>
  <joint name="RM_XI_JOINT" type="revolute">
    <origin xyz="0.043146 0 0.004675" rpy="0 0 -1.5708" />
    <parent link="RM_ZHOU_LINK" />
    <child link="RM_XI_LINK" />
    <axis xyz="0 0 1" />
    <limit lower="-1.5708" upper="1.5708" effort="0" velocity="0" />
  </joint>
  <link name="RM_R_LINK">
    <inertial>
      <origin xyz="-6.88468379528295E-18 0 -1.38777878078145E-17" rpy="0 0 0" />
      <mass value="5.23598775598299E-07" />
      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
    </inertial>
    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
  </link>
  <joint name="RM_R_JOINT" type="revolute">
    <origin xyz="0.10465 -5E-05 0" rpy="3.1416 1.5708 0" />
    <parent link="RM_XI_LINK" />
    <child link="RM_R_LINK" />
    <axis xyz="0 0 -1" />
    <limit lower="-1.5708" upper="1.5708" effort="0" velocity="0" />
  </joint>
  <link name="RM_P_LINK">
    <inertial>
      <origin xyz="1.38777878078145E-17 -2.77555756156289E-17 -6.88468379528295E-18" rpy="0 0 0" />
      <mass value="5.23598775598299E-07" />
      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
    </inertial>
    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
  </link>
  <joint name="RM_P_JOINT" type="revolute">
    <origin xyz="0 0 0" rpy="0 1.5708 0" />
    <parent link="RM_R_LINK" />
    <child link="RM_P_LINK" />
    <axis xyz="0 0 1" />
    <limit lower="-1.5708" upper="1.5708" effort="0" velocity="0" />
  </joint>
  <link name="RM_Y_LINK">
    <inertial>
      <origin xyz="1.38777878078145E-17 -9.05308814025396E-18 5.55111512312578E-17" rpy="0 0 0" />
      <mass value="5.23598775598299E-07" />
      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
    </inertial>
    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
  </link>
  <joint name="RM_Y_JOINT" type="revolute">
    <origin xyz="0 0 0" rpy="1.5708 0 0" />
    <parent link="RM_P_LINK" />
    <child link="RM_Y_LINK" />
    <axis xyz="0 0 -1" />
    <limit lower="-1.5708" upper="1.5708" effort="0" velocity="0" />
  </joint>
  <link name="RF_JIAN_LINK">
    <inertial>
      <origin xyz="0.0187543594239746 -0.000379261041653148 0.000812950580056213" rpy="0 0 0" />
      <mass value="0.006998228698532" />
      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
    </inertial>
    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
  </link>
  <joint name="RF_JIAN_JOINT" type="revolute">
    <origin xyz="0.077746 -0.036979 0.0047" rpy="0 0 -0.7854" />
    <parent link="base_link" />
    <child link="RF_JIAN_LINK" />
    <axis xyz="0 0 1" />
    <limit lower="-1.5708" upper="1.5708" effort="0" velocity="0" />
  </joint>
  <link name="RF_ZHOU_LINK">
    <inertial>
      <origin xyz="0.0212109520763576 -1.20023545394973E-05 0.00316723430018339" rpy="0 0 0" />
      <mass value="0.0234278880986834" />
      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
    </inertial>
    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
  </link>
  <joint name="RF_ZHOU_JOINT" type="revolute">
    <origin xyz="0.03995 0.0047 0" rpy="1.5708 0 0" />
    <parent link="RF_JIAN_LINK" />
    <child link="RF_ZHOU_LINK" />
    <axis xyz="0 0 1" />
    <limit lower="-1.5708" upper="1.5708" effort="0" velocity="0" />
  </joint>
  <link name="RF_XI_LINK">
    <inertial>
      <origin xyz="0.0466384689069635 -7.84328003208545E-05 0.000588778477364212" rpy="0 0 0" />
      <mass value="0.00724422084311935" />
      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
    </inertial>
    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
  </link>
  <joint name="RF_XI_JOINT" type="revolute">
    <origin xyz="0.043146 0 0.004675" rpy="0 0 -1.5708" />
    <parent link="RF_ZHOU_LINK" />
    <child link="RF_XI_LINK" />
    <axis xyz="0 0 1" />
    <limit lower="-1.5708" upper="1.5708" effort="0" velocity="0" />
  </joint>
  <link name="RF_R_LINK">
    <inertial>
      <origin xyz="5.55111512312578E-17 -1.23512311489549E-15 1.17961196366423E-15" rpy="0 0 0" />
      <mass value="5.23598775598299E-07" />
      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
    </inertial>
    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
  </link>
  <joint name="RF_R_JOINT" type="revolute">
    <origin xyz="0.10465 -5E-05 0" rpy="-1.5708 0.7854 1.5708" />
    <parent link="RF_XI_LINK" />
    <child link="RF_R_LINK" />
    <axis xyz="0 0 1" />
    <limit lower="-1.5708" upper="1.5708" effort="0" velocity="0" />
  </joint>
  <link name="RF_P_LINK">
    <inertial>
      <origin xyz="-7.35522753814166E-16 -7.07767178198537E-16 5.55111512312578E-17" rpy="0 0 0" />
      <mass value="5.23598775598299E-07" />
      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
    </inertial>
    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
  </link>
  <joint name="RF_P_JOINT" type="revolute">
    <origin xyz="0 0 0" rpy="0 1.5708 0" />
    <parent link="RF_R_LINK" />
    <child link="RF_P_LINK" />
    <axis xyz="0 0 1" />
    <limit lower="-1.5708" upper="1.5708" effort="0" velocity="0" />
  </joint>
  <link name="RF_Y_LINK">
    <inertial>
      <origin xyz="-1.17961196366423E-15 5.55111512312578E-17 1.23512311489549E-15" rpy="0 0 0" />
      <mass value="5.23598775598299E-07" />
      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
    </inertial>
    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
  </link>
  <joint name="RF_Y_JOINT" type="revolute">
    <origin xyz="0 0 0" rpy="1.5708 0 0" />
    <parent link="RF_P_LINK" />
    <child link="RF_Y_LINK" />
    <axis xyz="0 0 -1" />
    <limit lower="-1.5708" upper="1.5708" effort="0" velocity="0" />
  </joint>
  <link name="LF_JIAN_LINK">
    <inertial>
      <origin xyz="0.0187543594239746 -0.000379261041653173 0.000812950580056271" rpy="0 0 0" />
      <mass value="0.006998228698532" />
      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
    </inertial>
    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
  </link>
  <joint name="LF_JIAN_JOINT" type="revolute">
    <origin xyz="0.077746 0.036979 0.0047" rpy="0 0 0.7854" />
    <parent link="base_link" />
    <child link="LF_JIAN_LINK" />
    <axis xyz="0 0 1" />
    <limit lower="-1.5708" upper="1.5708" effort="0" velocity="0" />
  </joint>
  <link name="LF_ZHOU_LINK">
    <inertial>
      <origin xyz="0.0212109520763105 -1.20023545296362E-05 0.00316723430032838" rpy="0 0 0" />
      <mass value="0.0234278880989933" />
      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
    </inertial>
    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
  </link>
  <joint name="LF_ZHOU_JOINT" type="revolute">
    <origin xyz="0.03995 0.0047 0" rpy="1.5708 0 0" />
    <parent link="LF_JIAN_LINK" />
    <child link="LF_ZHOU_LINK" />
    <axis xyz="0 0 1" />
    <limit lower="-1.5708" upper="1.5708" effort="0" velocity="0" />
  </joint>
  <link name="LF_XI_LINK">
    <inertial>
      <origin xyz="0.046638468906964 -2.84328003209711E-05 0.000588778477360656" rpy="0 0 0" />
      <mass value="0.00724422084311936" />
      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
    </inertial>
    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
  </link>
  <joint name="LF_XI_JOINT" type="revolute">
    <origin xyz="0.043096 0 0.004675" rpy="0 0 -1.5708" />
    <parent link="LF_ZHOU_LINK" />
    <child link="LF_XI_LINK" />
    <axis xyz="0 0 1" />
    <limit lower="-1.5708" upper="1.5708" effort="0" velocity="0" />
  </joint>
  <link name="LF_R_LINK">
    <inertial>
      <origin xyz="5.55111512312578E-17 2.77555756156289E-17 4.16333634234434E-17" rpy="0 0 0" />
      <mass value="5.23598775598299E-07" />
      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
    </inertial>
    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
  </link>
  <joint name="LF_R_JOINT" type="revolute">
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

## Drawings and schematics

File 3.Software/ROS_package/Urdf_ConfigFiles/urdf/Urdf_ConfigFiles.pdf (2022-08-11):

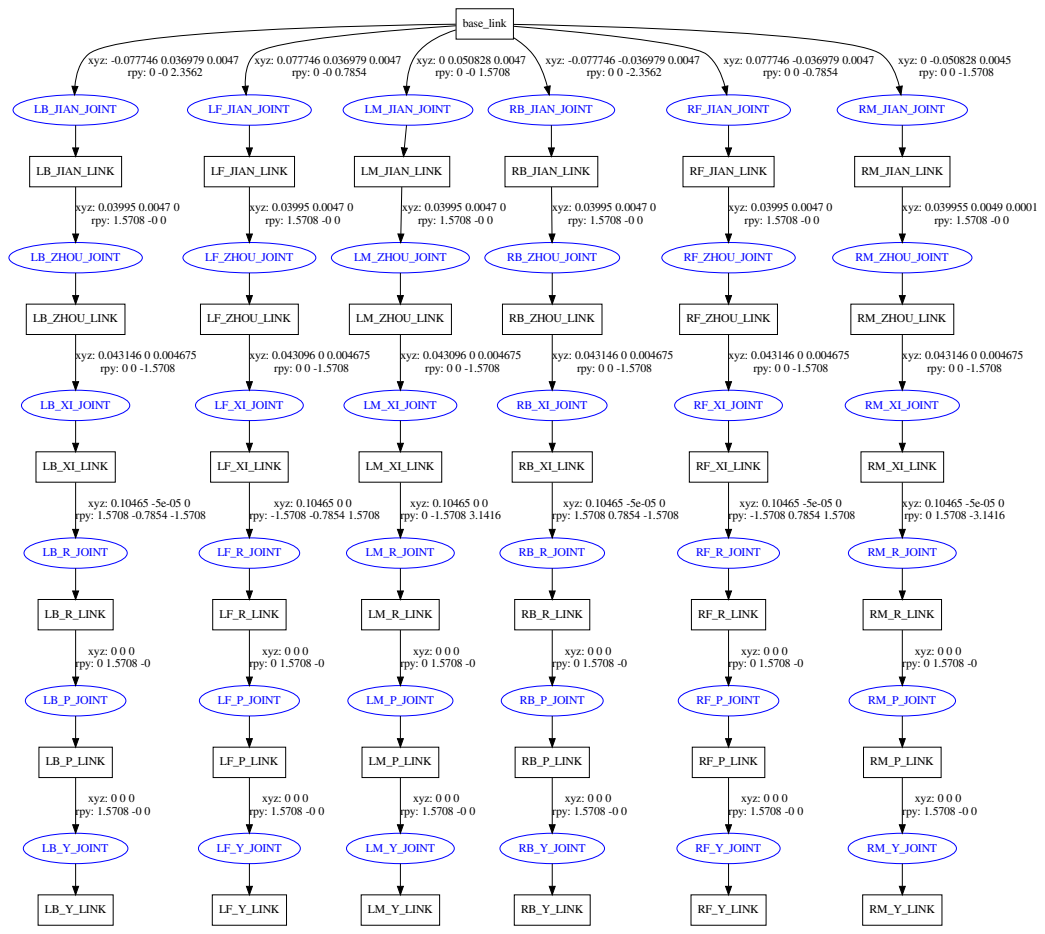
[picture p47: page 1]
base_link; LB_JIAN_JOINT; xyz: -0.077746 0.036979 0.0047 rpy: 0 -0 2.3562; LF_JIAN_JOINT; xyz: 0.077746 0.036979 0.0047 rpy: 0 -0 0.7854; LM_JIAN_JOINT; xyz: 0 0.050828 0.0047 rpy: 0 -0 1.5708; RB_JIAN_JOINT; xyz: -0.077746 -0.036979 0.0047 rpy: 0 0 -2.3562; RF_JIAN_JOINT; xyz: 0.077746 -0.036979 0.0047 rpy: 0 0 -0.7854; RM_JIAN_JOINT; xyz: 0 -0.050828 0.0045 rpy: 0 0 -1.5708; LB_JIAN_LINK; LB_ZHOU_JOINT; xyz: 0.03995 0.0047 0 rpy: 1.5708 -0 0; LB_ZHOU_LINK; LB_XI_JOINT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

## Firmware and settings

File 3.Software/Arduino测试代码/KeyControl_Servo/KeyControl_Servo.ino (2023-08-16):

/*******************************************************
   硬件：Baize_ServoDriver_esp32
   功能：KeyControl_Servo,通过按键校准机器人关节
   引脚：key1:35    key2:34    key3:39    key4:36
   Designer: Allen
   E-mail:953598974@qq.com
   Date:2022-09-20 16:39
*******************************************************/

#include <Wire.h>
#include <Adafruit_PWMServoDriver.h>
#include <SPI.h>
#include <TFT_eSPI.h>
//四个按键，按下后由低电平变为高电平
#define key1 35
#define key2 34
#define key3 39
#define key4 36

//#define SERVOMIN  102               //0.5/20 * 4096 = 102
//#define SERVOMID  307               //1.5/20 * 4096 = 307
//#define SERVOMAX  512               //2.5/20 * 4096 = 512
//实际测试
#define SERVOMIN  102               
#define SERVOMID  327               
#define SERVOMAX  552

Adafruit_PWMServoDriver pwm = Adafruit_PWMServoDriver();               //驱动1~16或(0~15)号舵机
Adafruit_PWMServoDriver pwm1 = Adafruit_PWMServoDriver(0x41);          //驱动17~32或(16~31)号舵机

TFT_eSPI TFT = TFT_eSPI();
//定义一个按键结构体，用于描述四个按键的各种属性和状态
struct keyStruct{
  String name;
  int pin;
  bool lastStatus;
};

keyStruct key[4]={
  "Key 1",35,0,
  "Key 2",34,0,
  "Key 3",39,0,
  "Key 4",36,0
};
//定义一个舵机结构体，用于描述32个舵机的各种属性和状态
struct servoStruct{
  String name;
  int num;
  bool lastStatus;
};

servoStruct servo[32]={
  "Servo 1:",SERVOMID,0,"Servo 2:",SERVOMID,0,"Servo 3:",SERVOMID,0,"Servo 4:",SERVOMID,0,
  "Servo 5:",SERVOMID,0,"Servo 6:",SERVOMID,0,"Servo 7:",SERVOMID,0,"Servo 8:",SERVOMID,0,
  "Servo 9:",SERVOMID,0,"Servo 10:",SERVOMID,0,"Servo 11:",SERVOMID,0,"Servo 12:",SERVOMID,0,
  "Servo 13:",SERVOMID,0,"Servo 14:",SERVOMID,0,"Servo 15:",SERVOMID,0,"Servo 16:",SERVOMID,0,
  "Servo 17:",SERVOMID,0,"Servo 18:",SERVOMID,0,"Servo 19:",SERVOMID,0,"Servo 20:",SERVOMID,0,
  "Servo 21:",SERVOMID,0,"Servo 22:",SERVOMID,0,"Servo 23:",SERVOMID,0,"Servo 24:",SERVOMID,0,
  "Servo 25:",SERVOMID,0,"Servo 26:",SERVOMID,0,"Servo 27:",SERVOMID,0,"Servo 28:",SERVOMID,0,
  "Servo 29:",SERVOMID,0,"Servo 30:",SERVOMID,0,"Servo 31:",SERVOMID,0,"Servo 32:",SERVOMID,0
};
//光标位置，一共四行，定义为0，1，2，3
int insert_f=0;
bool screen_update=0;//1为需要刷新屏幕，0为无需刷新屏幕

void setup() {
  // put your setup code here, to run once:
  //初始化串口
  Serial.begin(115200);
  Serial.print("Program:KeyControl_Servo!");
  //初始化舵机驱动
  pwm.begin();
  pwm1.begin();
  pwm.setPWMFreq(50);  // Analog servos run at ~50 Hz updates
  pwm1.setPWMFreq(50);  // Analog servos run at ~50 Hz updates
  //初始化显示屏
  TFT.init();
  TFT.setRotation(3);
  TFT.fillScreen(TFT_BLACK);
  TFT.initDMA();
  //设置4个按键为输入模式
  for(int i=0;i<4;i++)
    pinMode(key[i].pin,INPUT);

  screen_update = 1;
  
}

void loop() {
  // put your main code here, to run repeatedly:
    if(digitalRead(key[0].pin)==1)
    {
      delayMicroseconds(10);
      if(digitalRead(key[0].pin)==1)
      {
        if(key[0].lastStatus==0)
        {
          servo[insert_f].num++;
          servo[insert_f].num = (servo[insert_f].num)>SERVOMAX?SERVOMAX:servo[insert_f].num;
          key[0].lastStatus=1;
          screen_update = 1;
          Serial.println("hello1");
          delay(200);
        }
        else if(key[0].lastStatus==1)
        {
          Serial.println("hello2");
          servo[insert_f].num++;
          servo[insert_f].num = (servo[insert_f].num)>SERVOMAX?SERVOMAX:servo[insert_f].num;
          delay(60);
          screen_update = 1;
        }
      }
    }
    if(digitalRead(key[0].pin)==0)
    {
      delayMicroseconds(10);
      if(digitalRead(key[0].pin)==0)
      {
        if(key[0].lastStatus==1)
        {
          key[0].lastStatus=0;
        }
      }
    }
    
    if(digitalRead(key[1].pin)==1)
    {
      delayMicroseconds(10);
      if(digitalRead(key[1].pin)==1)
      {
        if(key[1].lastStatus==0)
        {
          servo[insert_f].num--;
          servo[insert_f].num = (servo[insert_f].num)<SERVOMIN?SERVOMIN:servo[insert_f].num;
          key[1].lastStatus=1;
          screen_update = 1;
          Serial.println("hello1");
          delay(200);
        }
        else if(key[1].lastStatus==1)
        {
          Serial.println("hello2");
          servo[insert_f].num--;
          servo[insert_f].num = (servo[insert_f].num)<SERVOMIN?SERVOMIN:servo[insert_f].num;
          delay(60);
          screen_update = 1;
        }
      }
    }
    if(digitalRead(key[1].pin)==0)
    {
      delayMicroseconds(10);
      if(digitalRead(key[1].pin)==0)
      {
        if(key[1].lastStatus==1)
        {
          key[1].lastStatus=0;
        }
      }
    }
    //key3：向上翻页
    if(digitalRead(key[2].pin)==1)
    {
      delayMicroseconds(10);
      if(digitalRead(key[2].pin)==1)
      {
        if(key[2].lastStatus==0)
        {
          if(insert_f==0)
          {
            insert_f=31;          
          }
          else
            insert_f--;

          screen_update = 1;
          key[2].lastStatus=1;
        }
      }
    }
    if(digitalRead(key[2].pin)==0)
    {
      delayMicroseconds(10);
      if(digitalRead(key[2].pin)==0)
      {
        if(key[2].lastStatus==1)
        {
          key[2].lastStatus=0;
        }
      }
    }
    //key4：向下翻页
    if(digitalRead(key[3].pin)==1)
    {
      delayMicroseconds(10);
      if(digitalRead(key[3].pin)==1)
      {
        if(key[3].lastStatus==0)
        {
          if(insert_f==31)
          {
            insert_f=0;            
          }
          else
            insert_f++;
 
          key[3].lastStatus=1;
          screen_update = 1;
        }
      }
    }
    if(digitalRead(key[3].pin)==0)
    {
      delayMicroseconds(10);
      if(digitalRead(key[3].pin)==0)
      {
        if(key[3].lastStatus==1)
        {
          key[3].lastStatus=0;
        }
      }
    }
  if(screen_update)
  {
    TFT.fillScreen(TFT_BLACK);
    for(int i=0;i<4;i++)
    {
      TFT.setCursor(10, 30*(i), 4);//前俩参数是位置(横纵坐标),第三个参数是字体大小
      TFT.setTextColor(TFT_WHITE, TFT_BLACK);
      TFT.println(servo[insert_f/4*4+i].name);
      TFT.drawNumber(servo[insert_f/4*4+i].num, 120, 30*(i));               // Draw float using current font 
    }
    TFT.setCursor(200, 30*(insert_f%4), 4);//前俩参数是位置(横纵坐标),第三个参数是字体大小
    TFT.setTextColor(TFT_WHITE, TFT_BLACK);
    TFT.println("<--");    
    screen_update = 0;
  }
  for(int servoi=0;servoi<16;servoi++)
    pwm.setPWM(servoi, 0, servo[servoi].num);
  for(int servoi=16;servoi<31;servoi++)
    pwm1.setPWM(servoi%16, 0, servo[servoi].num);
  delay(10);
  
}

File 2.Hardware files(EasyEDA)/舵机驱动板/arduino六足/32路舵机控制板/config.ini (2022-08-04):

[Config]
Lang=zh-CN
COM=COM28 (USB 串行设备)
Baud=19200
DelaySendTime=10
DonotTipAGF=0
FMQ=1
HID=0
ServoAngle=180
ServoShowAngle=0
Baud1=9600
Baud2=9600
Baud3=9600
Baud4=256000
ServoSet=#1SV0X5Y5P1500D0#2SV0X108Y5P1500D0#3SV0X210Y5P1500D0#4SV1X371Y258P1500D0#5SV1X464Y242P1500D0#6SV1X558Y255P1500D0#7SV1X371Y140P1471D-29#8SV1X464Y123P1500D0#9SV1X557Y144P1500D0#10SV1X372Y28P1441D-59#11SV1X464Y6P1529D29#12SV1X556Y28P1412D-88#13SV0X414Y95P1500D0#14SV0X516Y95P1500D0#15SV0X618Y95P1500D0#16SV0X720Y95P1500D0#17SV0X5Y185P1500D0#18SV0X108Y185P1500D0#19SV0X210Y185P1500D0#20SV0X312Y185P1500D0#21SV1X26Y25P1412D-88#22SV1X120Y6P1500D0#23SV1X213Y23P1500D0#24SV1X25Y129P1471D-29#25SV1X118Y116P1500D0#26SV1X212Y136P1500D0#27SV1X20Y257P1500D0#28SV1X114Y238P1500D0#29SV1X208Y251P1559D59#30SV0X516Y275P1500D0#31SV0X618Y275P1500D0#32SV0X720Y275P1500D0
ReferPosition=#1P1500#2P1500#3P1500#4P1500#5P1500#6P1500#7P1500#8P1500#9P1500#10P1500#11P1500#12P1500#13P1500#14P1500#15P1500#16P1500#17P1500#18P1500#19P1500#20P1500#21P1500#22P1500#23P1500#24P1500#25P1500#26P1500#27P1500#28P1500#29P1500#30P1500#31P1500#32P1500
FileList=Name:qj.txt--Size:306--Name:ht.txt--Size:306--Name:zz.txt--Size:306--Name:yz.txt--Size:306--
Servo1.Color=Cornflowerblue
Servo2.Color=Cornflowerblue
Servo3.Color=Cornflowerblue
Servo4.Color=Cornflowerblue
Servo5.Color=Cornflowerblue
Servo6.Color=Cornflowerblue
Servo7.Color=Cornflowerblue
Servo8.Color=Cornflowerblue
Servo9.Color=Darkorchid
Servo10.Color=Darkorchid
Servo11.Color=Darkorchid
Servo12.Color=Darkorchid
Servo13.Color=Darkorchid
Servo14.Color=Darkorchid
Servo15.Color=Darkorchid
Servo16.Color=Darkorchid
Servo17.Color=Darkseagreen
Servo18.Color=Darkseagreen
Servo19.Color=Darkseagreen
Servo20.Color=Darkseagreen
Servo21.Color=Darkseagreen
Servo22.Color=Darkseagreen
Servo23.Color=Darkseagreen
Servo24.Color=Darkseagreen
Servo25.Color=Lightskyblue
Servo26.Color=Lightskyblue
Servo27.Color=Lightskyblue
Servo28.Color=Lightskyblue
Servo29.Color=Lightskyblue
Servo30.Color=Lightskyblue
Servo31.Color=Lightskyblue
Servo32.Color=Lightskyblue

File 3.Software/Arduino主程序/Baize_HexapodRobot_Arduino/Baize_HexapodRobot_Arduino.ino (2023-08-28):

/*******************************************************
   主板：Baize_ServoDriver_esp8266
   功能：Baize_H1mini六足机器人Arduino程序
   引脚：SDA:21   SCL:22
   对于ARDUINO UNO，SCL:A5，SDA:A4
   Designer: Allen
   E-mail:953598974@qq.com
   Date:2022-08-22
*******************************************************/
#include <ESP8266WiFi.h>
#include <Wire.h>
#include <Adafruit_PWMServoDriver.h>
#include "StepData.h"
#define led 2               //led为低电平时，灯亮；高电平时，灯灭
#define MAX_SRV_CLIENTS 3   //最大同时联接数，即你想要接入的设备数量，8266tcpserver只能接入五个
#define del 100
#define deltr 3

const char *ssid = "Baize"; 
const char *password = "baizerobot"; 

Adafruit_PWMServoDriver pwm = Adafruit_PWMServoDriver();               //驱动1~16或(0~15)号舵机
Adafruit_PWMServoDriver pwm1 = Adafruit_PWMServoDriver(0x41);          //驱动17~32或(16~31)号舵机

WiFiServer server(8266);//你要的端口号，随意修改，范围0-65535
WiFiClient serverClients[MAX_SRV_CLIENTS];

//#define SERVOMIN  102               //0.5/20 * 4096 = 102
//#define SERVOMID  307               //1.5/20 * 4096 = 307
//#define SERVOMAX  512               //2.5/20 * 4096 = 512
//实际测试
#define SERVOMIN  102               
#define SERVOMID  327               
#define SERVOMAX  552

//pwm.setPWM(i, 0, pulselen);第一个参数是通道数;第二个是高电平起始点，也就是从0开始;第三个参数是高电平终止点。

//a:前进; b:后退; c:左转; d:右转; e:停止; f:向左横行 g:向右横行 h:步态切换 i:身高切换；
//last_cmd表示上一个指令，可以表示机器人状态。
char cmd = 'e',last_cmd = 'e';
//gait表示步态，1为波动步态，0为三角步态；body表示身高，0为最低，1为中间，2为最高;robotstatus为机器人状态，
int gait=0,body=0,robotstatus=0;
int rec[18] = {
  327,327,327,
  335,335,327,
  327,327,327,
  327,327,327,
  327,327,327,
  327,327,327
};
int direct[18] = {-1,1,1,
-1,1,1,
-1,1,1,
-1,1,1,
-1,1,1,
-1,1,1
};

//舵机执行函数，通过执行该函数，将会驱动18个舵机运动至s[18]数组传递的角度位置
void DireceServo(float s[18])
{
          for(int i=0;i<16;i++)
          {
            pwm.setPWM(i, 0, map(s[i]*direct[i],-90,90,-225,225)+rec[i]);
            
          }
          pwm1.setPWM(16-16, 0, map(s[16]*direct[16],-90,90,-225,225)+rec[16]);
          pwm1.setPWM(17-16, 0, map(s[17]*direct[17],-90,90,-225,225)+rec[17]);

          //如果想要更改舵机插口，需要写如下代码并把本函数内上方代码全部注释掉
          //舵机如果插在0-15号引脚，调用下面这个代码，m是板子上的接口号，i是机器人的关节号
          //pwm.setPWM(m, 0, map(s[i]*direct[i],-90,90,-225,225)+rec[i]);
          //舵机如果插在16-31号引脚，调用下面这个代码，m是板子上的接口号，i是机器人的关节号
          //pwm1.setPWM(m-16, 0, map(s[i]*direct[i],-90,90,-225,225)+rec[i]);
};

void iic_device_test()//扫描iic芯片，如果开机闪烁一次，说明是0x40未扫描到；如果闪烁两次，则是0x41未扫描到。
{
  bool iic_flag[2];//定义一个iic标志数组用于表示iic扫描结果
  Wire.beginTransmission(0x40);
  if(Wire.endTransmission()!=0)//0是扫描到设备了，非0是未扫描到设备。
  while(1)
  {
    digitalWrite(led,0);
    delay(100);
    digitalWrite(led,1);
    delay(1000);
  }
  Wire.beginTransmission(0x41);
  if(Wire.endTransmission()!=0)//0是扫描到设备了，非0是未扫描到设备。
  while(1)
  {
    digitalWrite(led,0);
    delay(100);
    digitalWrite(led,1);
    delay(100);
    digitalWrite(led,0);
    delay(100);
    digitalWrite(led,1);
    delay(1000);
  }
};

void setup() {
  // put your setup code here, to run once:
  pinMode(led, OUTPUT);
  digitalWrite(led, 1);//led为低电平时，灯亮；高电平时，灯灭
  Serial.begin(115200);
  Serial.println();
  Serial.println("Baize_HexapodRobot program!");

  Wire.begin();//开启IIC通信
  iic_device_test();
  
  
  pwm.begin();
  pwm1.begin();
  pwm.setPWMFreq(50);  // Analog servos run at ~50 Hz updates
  pwm1.setPWMFreq(50);  // Analog servos run at ~50 Hz updates

  
  
    for(int i=0;i<16;i++)
    {
      pwm.setPWM(i, 0, rec[i]);
      
    }
      pwm1.setPWM(0, 0, rec[16]);
      pwm1.setPWM(1, 0, rec[17]);
      ESP.wdtFeed();                    //喂狗防止复位
  delay(100);
  
  
  digitalWrite(led, 0);
  WiFi.begin(ssid, password);
  while (WiFi.status() != WL_CONNECTED)
  {
        delay(500);
        Serial.print(".");
  }
  server.begin();
  server.setNoDelay(true);  //加上后才正常些


  delay(1000);
  DireceServo(forward[0]);

}

void loop() {

    blink();
    
    uint8_t i;
    if (server.hasClient())
    {
        for (i = 0; i < MAX_SRV_CLIENTS; i++)
        {
            if (!serverClients[i] || !serverClients[i].connected())
            {
                if (serverClients[i]) serverClients[i].stop();//未联接,就释放
                serverClients[i] = server.available();//分配新的
                continue;
            }
 
        }
        WiFiClient serverClient = server.available();
        serverClient.stop();
    }
    for (i = 0; i < MAX_SRV_CLIENTS; i++)
    {
        if (serverClients[i] && serverClients[i].connected())
        {
            digitalWrite(led, 0);//有链接存在,就一直长亮
 
            if (serverClients[i].available())
            {
                while (serverClients[i].available()) 
                cmd = serverClients[i].read();
                delay(1);
                Serial.write(serverClients[i].read());
            }
        }
    }

    if(cmd == 'a')          //前进
    {
      if(gait==0)//如果是三角步态
      {
          for(int j=0;j<40;j++)
          {
              DireceServo(forward[j]);
              ESP.wdtFeed();                    //喂狗防止复位
              delay(deltr);
          }
      }
      else if(gait==1)//如果是波动步态
      {
          for(int j=0;j<120;j++)
          {
              DireceServo(forwardF[j]);
              ESP.wdtFeed();                    //喂狗防止复位
              delayMicroseconds(del);
          }
      }
//        for(int j=0;j<120;j++)
//          {
//              DireceServo(forwardF[j]);
//              ESP.wdtFeed();                    //喂狗防止复位
//              delayMicroseconds(del);
//          }
    }
    else if(cmd == 'b')//后退
    {
      if(gait==0)//如果是三角步态
      {
          for(int j=0;j<40;j++)
          {
              DireceServo(forward[39-j]);
              ESP.wdtFeed();                    //喂狗防止复位
              delay(deltr);
          }
      }
      else if(gait==1)//如果是波动步态
      {
          for(int j=0;j<120;j++)
          {
              DireceServo(forwardF[119-j]);
              ESP.wdtFeed();                    //喂狗防止复位
              delayMicroseconds(del);
          }
      }
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

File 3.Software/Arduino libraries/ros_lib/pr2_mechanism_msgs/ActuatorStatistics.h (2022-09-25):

#ifndef _ROS_pr2_mechanism_msgs_ActuatorStatistics_h
#define _ROS_pr2_mechanism_msgs_ActuatorStatistics_h

#include <stdint.h>
#include <string.h>
#include <stdlib.h>
#include "ros/msg.h"
#include "ros/time.h"

namespace pr2_mechanism_msgs
{

  class ActuatorStatistics : public ros::Msg
  {
    public:
      typedef const char* _name_type;
      _name_type name;
      typedef int32_t _device_id_type;
      _device_id_type device_id;
      typedef ros::Time _timestamp_type;
      _timestamp_type timestamp;
      typedef int32_t _encoder_count_type;
      _encoder_count_type encoder_count;
      typedef float _encoder_offset_type;
      _encoder_offset_type encoder_offset;
      typedef float _position_type;
      _position_type position;
      typedef float _encoder_velocity_type;
      _encoder_velocity_type encoder_velocity;
      typedef float _velocity_type;
      _velocity_type velocity;
      typedef bool _calibration_reading_type;
      _calibration_reading_type calibration_reading;
      typedef bool _calibration_rising_edge_valid_type;
      _calibration_rising_edge_valid_type calibration_rising_edge_valid;
      typedef bool _calibration_falling_edge_valid_type;
      _calibration_falling_edge_valid_type calibration_falling_edge_valid;
      typedef float _last_calibration_rising_edge_type;
      _last_calibration_rising_edge_type last_calibration_rising_edge;
      typedef float _last_calibration_falling_edge_type;
      _last_calibration_falling_edge_type last_calibration_falling_edge;
      typedef bool _is_enabled_type;
      _is_enabled_type is_enabled;
      typedef bool _halted_type;
      _halted_type halted;
      typedef float _last_commanded_current_type;
      _last_commanded_current_type last_commanded_current;
      typedef float _last_commanded_effort_type;
      _last_commanded_effort_type last_commanded_effort;
      typedef float _last_executed_current_type;
      _last_executed_current_type last_executed_current;
      typedef float _last_executed_effort_type;
      _last_executed_effort_type last_executed_effort;
      typedef float _last_measured_current_type;
      _last_measured_current_type last_measured_current;
      typedef float _last_measured_effort_type;
      _last_measured_effort_type last_measured_effort;
      typedef float _motor_voltage_type;
      _motor_voltage_type motor_voltage;
      typedef int32_t _num_encoder_errors_type;
      _num_encoder_errors_type num_encoder_errors;

    ActuatorStatistics():
      name(""),
      device_id(0),
      timestamp(),
      encoder_count(0),
      encoder_offset(0),
      position(0),
      encoder_velocity(0),
      velocity(0),
      calibration_reading(0),
      calibration_rising_edge_valid(0),
      calibration_falling_edge_valid(0),
      last_calibration_rising_edge(0),
      last_calibration_falling_edge(0),
      is_enabled(0),
      halted(0),
      last_commanded_current(0),
      last_commanded_effort(0),
      last_executed_current(0),
      last_executed_effort(0),
      last_measured_current(0),
      last_measured_effort(0),
      motor_voltage(0),
      num_encoder_errors(0)
    {
    }

    virtual int serialize(unsigned char *outbuffer) const
    {
      int offset = 0;
      uint32_t length_name = strlen(this->name);
      varToArr(outbuffer + offset, length_name);
      offset += 4;
      memcpy(outbuffer + offset, this->name, length_name);
      offset += length_name;
      union {
        int32_t real;
        uint32_t base;
      } u_device_id;
      u_device_id.real = this->device_id;
      *(outbuffer + offset + 0) = (u_device_id.base >> (8 * 0)) & 0xFF;
      *(outbuffer + offset + 1) = (u_device_id.base >> (8 * 1)) & 0xFF;
      *(outbuffer + offset + 2) = (u_device_id.base >> (8 * 2)) & 0xFF;
      *(outbuffer + offset + 3) = (u_device_id.base >> (8 * 3)) & 0xFF;
      offset += sizeof(this->device_id);
      *(outbuffer + offset + 0) = (this->timestamp.sec >> (8 * 0)) & 0xFF;
      *(outbuffer + offset + 1) = (this->timestamp.sec >> (8 * 1)) & 0xFF;
      *(outbuffer + offset + 2) = (this->timestamp.sec >> (8 * 2)) & 0xFF;
      *(outbuffer + offset + 3) = (this->timestamp.sec >> (8 * 3)) & 0xFF;
      offset += sizeof(this->timestamp.sec);
      *(outbuffer + offset + 0) = (this->timestamp.nsec >> (8 * 0)) & 0xFF;
      *(outbuffer + offset + 1) = (this->timestamp.nsec >> (8 * 1)) & 0xFF;
      *(outbuffer + offset + 2) = (this->timestamp.nsec >> (8 * 2)) & 0xFF;
      *(outbuffer + offset + 3) = (this->timestamp.nsec >> (8 * 3)) & 0xFF;
      offset += sizeof(this->timestamp.nsec);
      union {
        int32_t real;
        uint32_t base;
      } u_encoder_count;
      u_encoder_count.real = this->encoder_count;
      *(outbuffer + offset + 0) = (u_encoder_count.base >> (8 * 0)) & 0xFF;
      *(outbuffer + offset + 1) = (u_encoder_count.base >> (8 * 1)) & 0xFF;
      *(outbuffer + offset + 2) = (u_encoder_count.base >> (8 * 2)) & 0xFF;
      *(outbuffer + offset + 3) = (u_encoder_count.base >> (8 * 3)) & 0xFF;
      offset += sizeof(this->encoder_count);
      offset += serializeAvrFloat64(outbuffer + offset, this->encoder_offset);
      offset += serializeAvrFloat64(outbuffer + offset, this->position);
      offset += serializeAvrFloat64(outbuffer + offset, this->encoder_velocity);
      offset += serializeAvrFloat64(outbuffer + offset, this->velocity);
      union {
        bool real;
        uint8_t base;
      } u_calibration_reading;
      u_calibration_reading.real = this->calibration_reading;
      *(outbuffer + offset + 0) = (u_calibration_reading.base >> (8 * 0)) & 0xFF;
      offset += sizeof(this->calibration_reading);
      union {
        bool real;
        uint8_t base;
      } u_calibration_rising_edge_valid;
      u_calibration_rising_edge_valid.real = this->calibration_rising_edge_valid;
      *(outbuffer + offset + 0) = (u_calibration_rising_edge_valid.base >> (8 * 0)) & 0xFF;
      offset += sizeof(this->calibration_rising_edge_valid);
      union {
        bool real;
        uint8_t base;
      } u_calibration_falling_edge_valid;
      u_calibration_falling_edge_valid.real = this->calibration_falling_edge_valid;
      *(outbuffer + offset + 0) = (u_calibration_falling_edge_valid.base >> (8 * 0)) & 0xFF;
      offset += sizeof(this->calibration_falling_edge_valid);
      offset += serializeAvrFloat64(outbuffer + offset, this->last_calibration_rising_edge);
      offset += serializeAvrFloat64(outbuffer + offset, this->last_calibration_falling_edge);
      union {
        bool real;
        uint8_t base;
      } u_is_enabled;
      u_is_enabled.real = this->is_enabled;
      *(outbuffer + offset + 0) = (u_is_enabled.base >> (8 * 0)) & 0xFF;
      offset += sizeof(this->is_enabled);
      union {
        bool real;
        uint8_t base;
      } u_halted;
      u_halted.real = this->halted;
      *(outbuffer + offset + 0) = (u_halted.base >> (8 * 0)) & 0xFF;
      offset += sizeof(this->halted);
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

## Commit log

2022-08-04 First upload
    [Battery.SLDPRT, Battery_box.SLDPRT, Battery_box_cover.SLDPRT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]
2022-08-05 add urdf config files for ros
    [LB_JIAN_LINK.STL, LB_P_LINK.STL, LB_R_LINK.STL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]
2022-08-05 update 3D model
    [Body_link.SLDASM, Connecting_piece_12.DWG, Connecting_piece_12.STL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]
2022-08-05 fix a urdf file bug
    [Urdf_ConfigFiles.urdf]
2022-08-05 update model
    [robot_sixfoot.SLDASM]
2022-08-11 update kinetic source code
    [Urdf_ConfigFiles.urdf]
2022-08-24 Add arduino program
2022-08-25 Add 3D printer version model
    [Baize_HexapodRobot_Arduino_3DPrinter.STEP, Battery.SLDPRT, Battery_box.SLDPRT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]
2022-08-27 add the pcb board files for this robot
2022-08-27 add some photos for the main board
2022-08-27 add stl files to 3D print
    [body_back_wall_1.STL, body_bottom_1.SLDPRT, body_bottom_1.STL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]
2022-08-27 add the BOM for this robot
    [BOM.xlsx]
2022-08-30 update arduino program
2022-09-01 update the 3D model
    [dianpian.SLDPRT, ding.SLDPRT, foot.SLDPRT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]
2022-09-03 update Bom
    [BOM.xlsx]
2022-09-03 add the original 3D model
    [MG90S.SLDPRT, body.SLDASM, body_back_wall.SLDPRT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]
2022-09-15 add a ros package
    [LB_JIAN_LINK.STL, LB_P_LINK.STL, LB_R_LINK.STL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]
2022-09-16 add a ros package to publish joint data for arduino
2022-09-16 add a arduino program to subscribe joint topic for baize_servodriver_esp8266
2023-04-28 添加制作教程文件
2023-07-14 更新制作说明文档
2023-07-14 更新模型
    [MG90S.SLDPRT, body_back_wall.SLDPRT, body_bottom.SLDPRT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]
2023-07-26 更新3D打印模型
    [BATTERY HOLDER x2 18650.SLDASM, LM2596 DC-DC stepdown voltage converter.SLDPRT, body_bottom1.SLDPRT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]
2023-07-27 更新3D模型文件
    [body_bottom1.SLDPRT, joint.SLDASM, joint_bottom.SLDPRT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]
2023-07-27 更新并添加代码
2023-08-01 更新代码
2023-08-12 添加制作教程
2023-08-16 标定代码
2023-09-03 添加新版硬件
2023-10-21 更新制作文档
2023-10-24 更新制作教程
2023-11-06 更新硬件
2023-12-11 添加ROS版教程
2023-12-11 更新教程
